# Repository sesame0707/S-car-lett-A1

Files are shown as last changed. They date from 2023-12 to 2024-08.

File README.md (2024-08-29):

# S(car)lett A1

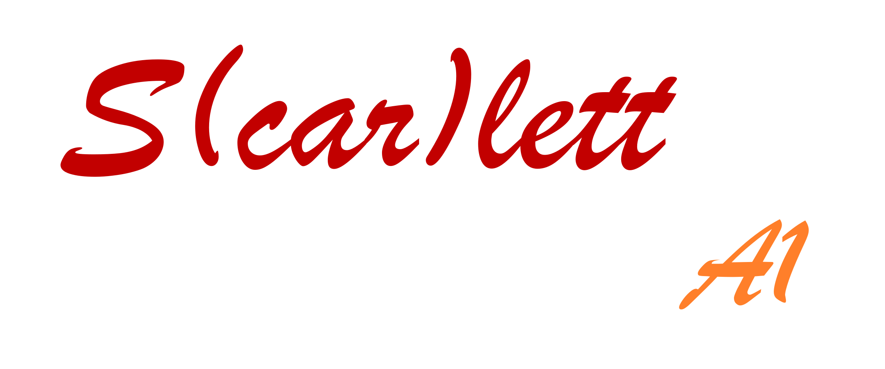
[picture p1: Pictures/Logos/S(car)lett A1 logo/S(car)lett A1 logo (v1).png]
S(car)lett A1 Logo


## The Repository
This is the repository of the first A-line car in the [`S(car)lett`](https://github.com/sesame0707/S-car-lett) project.

## High-Level Goals
Those are the initial goals of this module:
- The use of mechanical mechanisms implemented in the LEGO 8070 set
- Design focused on easy disassembly and assembly (reusable design)
- The use of more expensive, but desirable components instead of cheaper, but weaker ones

All of the above goals have been achieved throughout this module's implementation.

## Results
The car looks as follows:

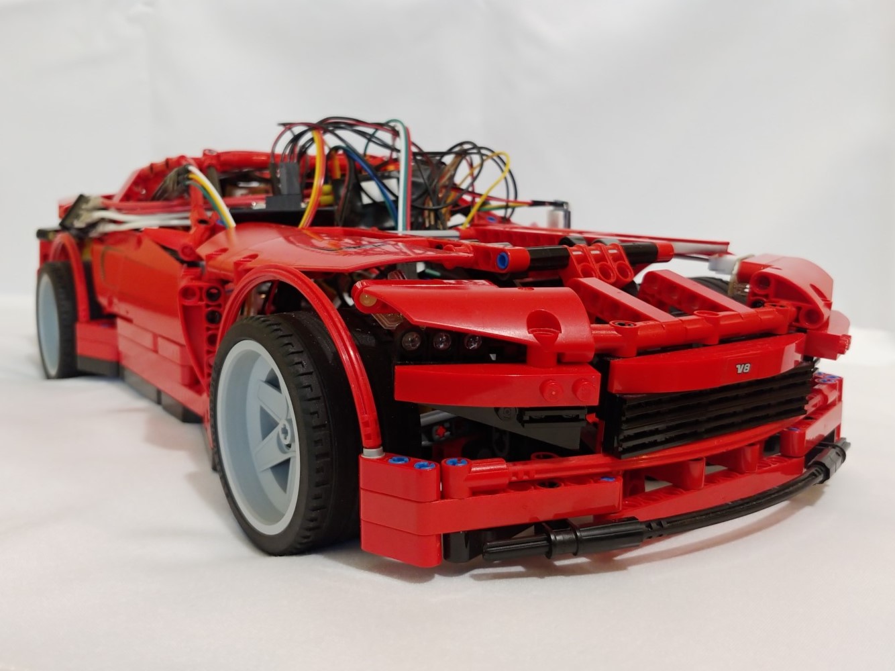
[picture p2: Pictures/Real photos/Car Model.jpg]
Car Model


It has some custom and standard electronic parts in it. The real photos of them can be accessed in the `Pictures/Real photos` folder. For the standard parts, refer to the table of parts that can be found in the `Documentation/General` folder. Moreover, this model also incorporates 3D-printed parts, which can be accessed in the `3D printed parts` folder.

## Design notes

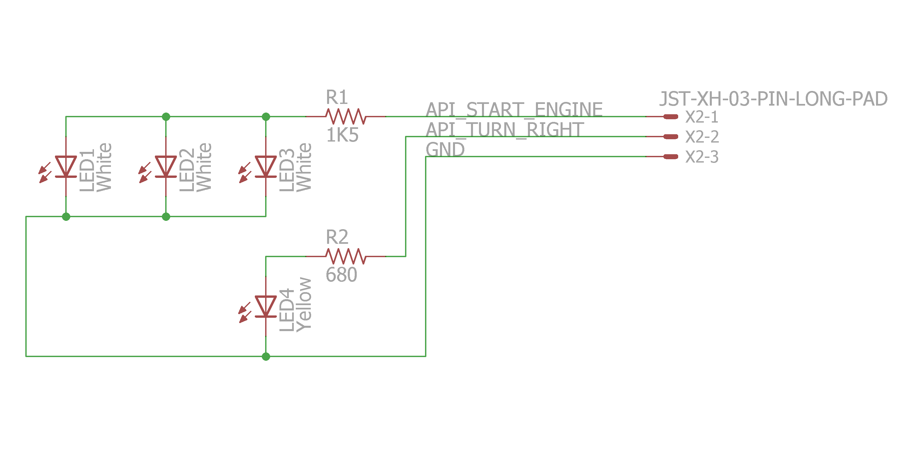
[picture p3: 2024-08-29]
Pictures/Electronic parts/Front Right Lamp (Schematic).png

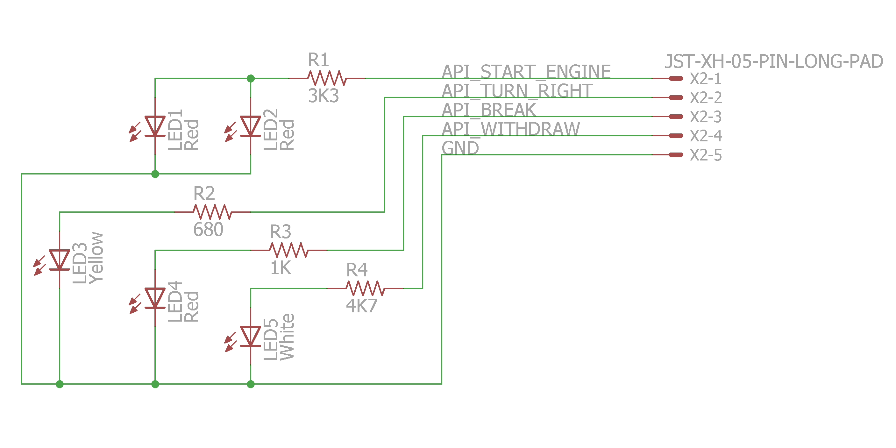
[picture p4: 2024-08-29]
Pictures/Electronic parts/Rear Right Lamp (Schematic).png

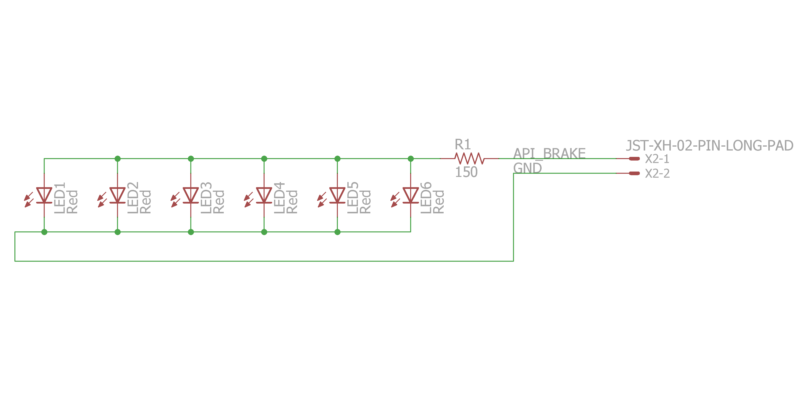
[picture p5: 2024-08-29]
Pictures/Electronic parts/Rear Brake Lamp (Schematic).png

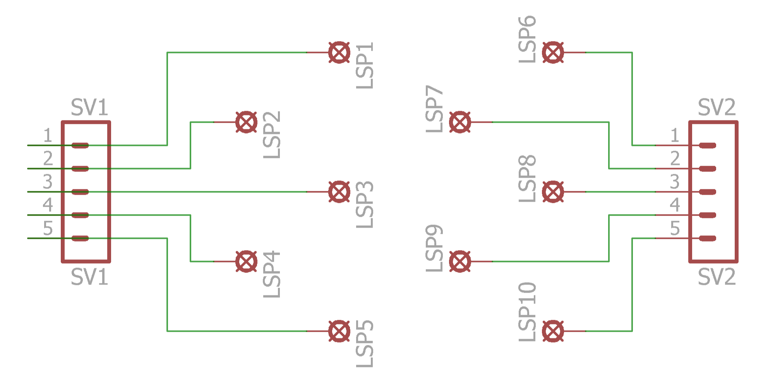
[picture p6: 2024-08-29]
Pictures/Electronic parts/Fuse Protector (Schematic).png

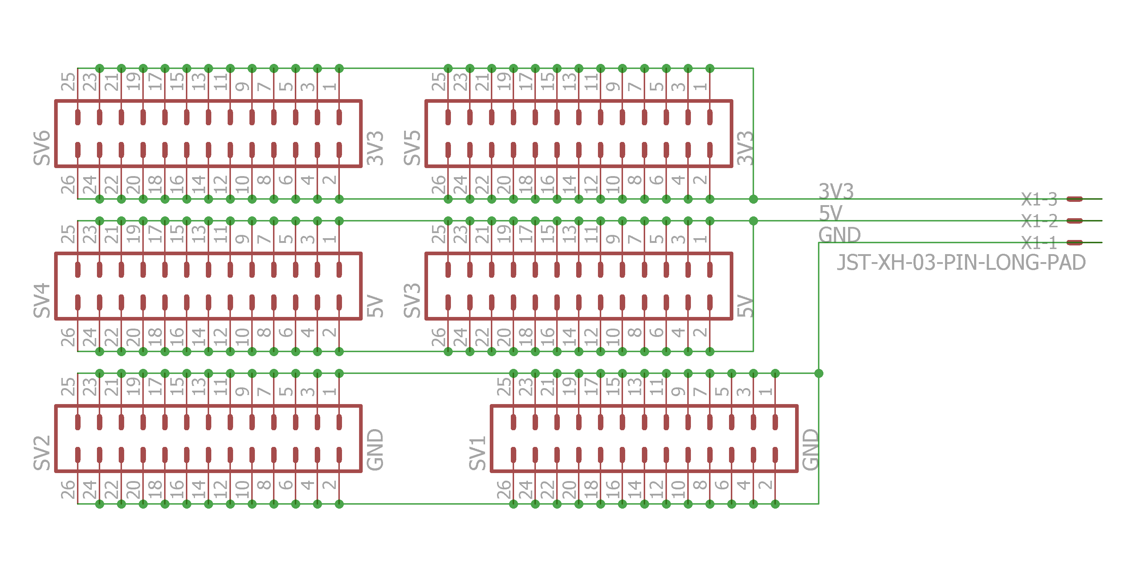
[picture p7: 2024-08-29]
Pictures/Electronic parts/STM32 Power Expander (Schematic).png

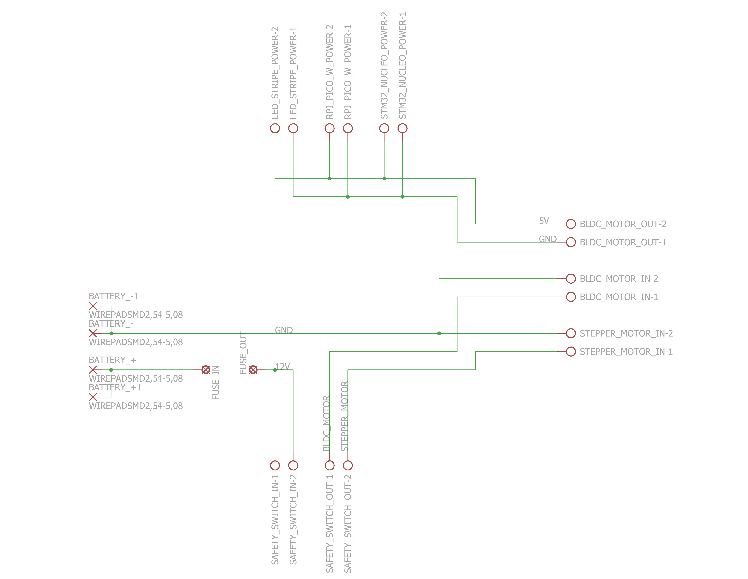
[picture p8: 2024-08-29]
Pictures/Electronic parts/Power Section (Schematic).png

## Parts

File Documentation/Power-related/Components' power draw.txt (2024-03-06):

Stepper motor
-------------
Inactive:		0.22 A @ 11 V = 2.42 W
Active:			0.72 A @ 11 V = 7.92 W

BLDC motor
----------
Without load:
-2 gear:		0.20 A @ 11 V = 2.20 W
-1 gear:		0.17 A @ 11 V = 1.87 W
0 gear:			0.01 A @ 11 V = 0.11 W
1 gear:			0.17 A @ 11 V = 1.87 W
2 gear:			0.20 A @ 11 V = 2.20 W
3 gear:			0.26 A @ 11 V = 2.86 W
4 gear:			0.27 A @ 11 V = 2.97 W

With load:		<= 0.50 A @ 11 V = 5.50 W

Voltmeter
---------
19.00 mA @ 12.60 V = 0.24 W
16.50 mA @ 11.00 V = 0.18 W
22.50 mA @ 9.00 V = 0.20 W

Battery level indicator
-----------------------
4.85 mA @ 12.60 V = 0.06 W
4.75 mA @ 11.00 V = 0.05 W
3.50 mA @ 9.00 V = 0.03 W

STM32 Nucleo
------------
Under load:		500 mA (?) @ 5 V = 2.50 W

	Lamps
	-----
	Start engine: 		1.6 mA
	Turn left: 		4.0 mA
	Turn right: 		4.0 mA
	Brake: 			12.0 mA
	Withdraw: 		0.3 mA
	
	All lamps:		21.9 mA @ 3.3 V = 0.07 W

RPi Pico W
----------
Under load:		100 mA @ 5 V = 0.50 W

LED stripes
-----------
All 14x sub-LEDs:	0.43 A @ 5 V = 2.15 W

Rechargeable battery
--------------------
Brand:			Sunpadow
Type:			Li-Po
Energy capacity:	24.98 Wh
Charge capacity:	2250 mAh
Cells:			3S-ERC
Maximum power output:	60C
Charge power input:	1C
Nominal total voltage:	11.1 V
Allowed total voltage:	9.0 V - 12.6 V

Current x charge level
----------------------
0 % (9.0 V):		1.52 A + 0.60 A = 2.12 A
25 % (10.2 V):		1.35 A + 0.53 A = 1.88 A
50 % (10.8 V):		1.27 A + 0.50 A = 1.77 A
75 % (11.4 V):		1.21 A + 0.47 A = 1.68 A
100 % (12.6 V):		1.10 A + 0.43 A = 1.53 A

Recommended fuses
-----------------
11 V main line:		2.50 A
5 V main line:		1.25 A
5 V STM32 line:		0.25 A
3.3 V STM32 line:	0.25 A

Summary
-------
Maximum total power draw:		13.72 W (11 V main line) + 5.40 W (?) (5 V main line) = 18.82 W
Theoretical minimum working time:	1.33 h (1 h 20 min) (?)
Theoretical average working time:	2.66 h (2 h 40 min) (?)

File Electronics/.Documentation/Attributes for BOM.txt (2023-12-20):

Attributes for BOM
Common:-----------------
MANUFACTURER
	LUCKYLIGHT
	ROYAL OHM
MANUFACTURER_PART_NUMBER
SUPPLIER
	TME
SUPPLIER_PART_NUMBER
SUPPLIER_URL

LED-specific:-----------
COLOR
CURRENT_EMPIRICAL
VOLTAGE_EMPIRICAL

Resistor-specific:------
RESISTANCE

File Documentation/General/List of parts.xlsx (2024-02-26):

PART NAME | QTY. | STATUS | PRICE (1 PCS.) | PRICE (ALL PCS.) | PRICE DATE | LINK | SELLER | PROJECT PRICE
LEGO 8070 "Supercar" set | 1 | Ready | 400.00 zł | 400.00 zł | 2011-07-07 | https://www.ceneo.pl/9803476 | Authorized LEGO reseller | 1849.65 zł
Nema 17 (23,5 mm) stepper motor | 1 | Ready | 35.00 zł | 35.00 zł | 2023-05-06 | https://allegro.pl/oferta/silnik-krokowy-nema17-17hs4023-z-kablem-1m-prusa-13093450848 | Allegro (sklep_X3D)
TMC2209 stepper motor driver | 1 | Ready | 28.50 zł | 28.50 zł | 2023-05-06 | https://allegro.pl/oferta/sterownik-silnika-krokowego-tmc2209-v1-3-stepstick-13629864488 | Allegro (sklep_X3D)
GT2 belt (6 mm, 1 m) | 1 | Ready | 6.99 zł | 6.99 zł | 2023-05-06 | https://allegro.pl/oferta/pasek-zebaty-gumowy-gt2-6mm-napedowy-cnc-100cm-12872474627 | Allegro (sklep_X3D)
GT2 overlay for stepper motor (20 T, 10 mm) | 1 | Ready | 9.90 zł | 9.90 zł | 2023-05-06 | https://allegro.pl/oferta/kolo-pasowe-zebate-20-zebow-otwor-6mm-gt2-10mm-12588977251 | Allegro (sklep_X3D)
Zip ties (2,5 mm x 100 mm ⌀ 3 mm 100 pcs.) | 1 | Ready | 2.69 zł | 2.69 zł | 2023-07-17 | https://allegro.pl/oferta/opaski-zaciskowe-kablowe-trytytki-100x2-5mm-100szt-13133446154 | Allegro (sklep_X3D)
Nema 17 radiator | 1 | Ready | 6.99 zł | 6.99 zł | 2023-07-17 | https://allegro.pl/oferta/radiator-silnika-krokowego-40x40x11-czarny-nema17-12867637945 | Allegro (sklep_X3D)
Coupler (5 mm, 8 mm) | 1 | Ready | 5.99 zł | 5.99 zł | 2023-07-17 | https://allegro.pl/oferta/sprzeglo-elastyczne-5x8-aluminiowe-cnc-13094635538 | Allegro (sklep_X3D)
STM32 NUCLEO-F767ZI developer board | 1 | Ready | 145.00 zł | 145.00 zł | 2023-08-10 | https://allegro.pl/oferta/stm32-nucleo-f767zi-stm32f767zit6-arm-cortex-m7-14034014339 | Allegro (botland_pl)
JST-SM 2/3/4/5 pin header set | 1 | Ready | 31.00 zł | 31.00 zł | 2023-08-17 | https://allegro.pl/oferta/zestaw-zlacz-justpi-jst-sm-2-3-4-5pin-11787730550 | Allegro (botland_pl)
USB A male connector (5 pcs.) | 1 | Ready | 3.00 zł | 3.00 zł | 2023-08-17 | https://allegro.pl/oferta/gniazdo-usb-typu-a-zenskie-tht-5szt-12551145487 | Allegro (botland_pl)
USB micro B - USB A 2.0 (0,15 m) cable | 1 | Ready | 4.00 zł | 4.00 zł | 2023-08-17 | https://allegro.pl/oferta/przewod-microusb-b-usb-a-2-0-hi-speed-0-15-m-14012907744 | Allegro (botland_pl)
WS2812B LED stripe (60 LED/m, IP65, 1 m) | 1 | Ready | 32.90 zł | 32.90 zł | 2023-08-17 | https://allegro.pl/oferta/tasma-led-adresowalna-ws2812b-argb-60led-m-ip65-13796044103 | Allegro (Minosalis)
JST-SM 3 pin LED male and female cable set (15 cm) | 4 | Ready | 3.50 zł | 14.00 zł | 2023-08-17 | https://allegro.pl/oferta/wtyczka-jst-sm-3-pin-led-argb-meska-i-zenska-15-cm-13821206609 | Allegro (Minosalis)
JST-SM 3 pin LED splitter (15 cm) | 1 | Ready | 10.90 zł | 10.90 zł | 2023-08-17 | https://allegro.pl/oferta/rozdzielacz-jst-sm-3-pin-do-led-argb-13821309653 | Allegro (Minosalis)
Imax B6AC 80W charger | 1 | Ready | 134.78 zł | 134.78 zł | 2023-08-17 | https://allegro.pl/oferta/ladowarka-b6ac-z-balanserem-do-pakietow-13584815585 | Allegro (kamami_pl)
Sunpadow Li-Po battery (3S, 11,1 V, 60 C, 2250 mAh, XT60) | 1 | Ready | 104.57 zł | 104.57 zł | 2023-08-17 | https://www.amazon.pl/dp/B08S3C9C5M?psc=1&ref=ppx_yo2ov_dt_b_product_details | Amazon (Xiamen 3-circles Battery Co., Ltd.)
40A ESC and 1000KV BLDC motor set | 1 | Ready | 73.55 zł | 73.55 zł | 2023-08-17 | https://www.amazon.pl/gp/product/B08T6CNVQT/ref=ppx_od_dt_b_asin_title_s00?ie=UTF8&psc=1 | Amazon (Yisteel-EU)
VL53L1X ToF module | 4 | Ready | 19.39 zł | 77.56 zł | 2023-09-04 | https://pl.aliexpress.com/item/4000074204979.html | AliExpress (SAMIORE Store)
Electric cubes (12 x 2,5 mm2) | 3 | Ready | 1.57 zł | 4.71 zł | 2023-09-04 | https://allegro.pl/oferta/listwa-zaciskowa-zlaczka-kostka-12-torowa-2-5mm2-8501387810 | Allegro (electro_24)
Electric cubes (12 x 4 mm2) | 1 | Ready | 1.89 zł | 1.89 zł | 2023-09-04 | https://allegro.pl/oferta/zlaczka-listwa-instalacyjna-kablowa-12-torowa-4mm-7270241593 | Allegro (electro_24)
Tubular terminals set | 1 | Ready | 54.90 zł | 54.90 zł | 2023-09-04 | https://allegro.pl/oferta/zaciskarka-do-konektorow-koncowek-500-tulejek-13993749597 | Allegro (electro_24)
Universal PCB set | 1 | Ready | 33.99 zł | 33.99 zł | 2023-09-04 | https://www.amazon.pl/gp/product/B07V25W5RT | Amazon (AZDelivery)
IR module set | 1 | Ready | 20.49 zł | 20.49 zł | 2023-09-04 | https://www.amazon.pl/gp/product/B07V9XD2R6 | Amazon (AZDelivery)
Raspberry Pi Pico W enclosure (transparent) | 1 | Ready | 6.90 zł | 6.90 zł | 2023-09-12 | https://allegro.pl/oferta/obudowa-raspberry-pi-pico-transparentna-13052332067 | Allegro (Platet-A)
Security ON/OFF switch | 1 | Ready | 4.00 zł | 4.00 zł | 2023-09-12 | https://allegro.pl/oferta/przelacznik-klawiszowy-on-off-250v-kcd1-104-6a-12386835341 | Allegro (Platet-A)
OLED display (I2C, 0.96 in) | 1 | Ready | 20.00 zł | 20.00 zł | 2023-09-12 | https://allegro.pl/oferta/wyswietlacz-oled-0-96-cala-i2c-iic-4-pin-bialy-13396251090 | Allegro (Platet-A)
XT60 male connector with AWG12 wires | 1 | Ready | 15.50 zł | 15.50 zł | 2023-09-12 | https://allegro.pl/oferta/wtyk-xt60-meski-z-przewodem-10cm-awg12-14093751536 | Allegro (Platet-A)
XT60 female connector with AWG12 wires | 1 | Ready | 15.50 zł | 15.50 zł | 2023-09-12 | https://allegro.pl/oferta/gniazdo-xt60-z-przewodem-10cm-awg12-zenskie-14091453758 | Allegro (Platet-A)
LED diodes set (100 pcs.) | 1 | Ready | 12.00 zł | 12.00 zł | 2023-09-12 | https://allegro.pl/oferta/zestaw-diod-led-5mm-rgb-biale-100szt-mix-13396031473 | Allegro (Platet-A)
ARK 3 pin connector | 10 | Ready | 1.50 zł | 15.00 zł | 2023-09-12 | https://allegro.pl/oferta/konektor-listwa-ak-ark-5-0mm-h-10mm-3-pin-x-2szt-10420014477 | Allegro (Platet-A)
Male goldpin (2,54mm, 2x40) | 2 | Ready | 3.00 zł | 6.00 zł | 2023-09-12 | https://allegro.pl/oferta/listwa-gold-pin-2x40-meska-tht-2-54mm-prosta-10248104944 | Allegro (Platet-A)
Female goldpin (2,54mm, 1x40) | 4 | Ready | 3.00 zł | 12.00 zł | 2023-09-12 | https://allegro.pl/oferta/gniazdo-szplikowe-goldpin-raster-2-54mm-1x40-10248060552 | Allegro (Platet-A)
Resistors set (700 pcs.) | 1 | Ready | 22.90 zł | 22.90 zł | 2023-09-12 | https://allegro.pl/oferta/zestaw-rezystorow-przewlekanych-0-25w-1-700-sztuk-13498410400 | Allegro (Platet-A)
Female goldpin (2,54mm, 2x40) | 2 | Ready | 1.30 zł | 2.60 zł | 2023-10-19 | https://allegro.pl/oferta/listwa-goldpin-2x40-zenska-raster-2-54mm-10szt-12327613595 | Allegro (botland_pl)
Male goldpin (2,54mm, 2x40, curved) | 2 | Ready | 2.00 zł | 4.00 zł | 2023-10-19 | https://allegro.pl/oferta/wtyk-goldpin-2x40-katowy-raster-2-54mm-14376476217 | Allegro (botland_pl)
JST-XH 2-5 pin connector set (230 pcs.) | 1 | Ready | 25.00 zł | 25.00 zł | 2023-10-19 | https://allegro.pl/oferta/zestaw-zlacz-jst-xh2-54-meskie-zenskie-i-pinow-11032577415 | Allegro (botland_pl)
JST-XH 6-10 pin connector set (260 pcs.) | 1 | Ready | 31.00 zł | 31.00 zł | 2023-10-19 | https://allegro.pl/oferta/zestaw-zlacz-jst-xh2-54-6-7-8-9-10-pin-2-54mm-12635826639 | Allegro (botland_pl)
Male goldpin (2,54mm, 1x40, curved) | 4 | Ready | 2.00 zł | 8.00 zł | 2023-10-19 | https://allegro.pl/oferta/goldpin-czarny-1x40-szpil-katowy-raster-2-54mm-13410442465 | Allegro (kamami_pl)
Male goldpin (2,54mm, 1x40) | 4 | Ready | 1.70 zł | 6.80 zł | 2023-10-19 | https://allegro.pl/oferta/goldpin-czarny-1x40-szpil-prosty-raster-2-54mm-13717595094 | Allegro (kamami_pl)
VL53L1X ToF module | 4 | Ready | 17.57 zł | 70.28 zł | 2023-11-27 | https://pl.aliexpress.com/item/4000074204979.html | AliExpress (SAMIORE Store)
ZS-X10 V3 BLDC motor driver | 1 | Ready | 44.75 zł | 44.75 zł | 2023-12-01 | https://allegro.pl/oferta/sterownik-silnikow-bldc-6-20v-3a-13359462424 | Allegro (kamami_pl)
PTF-76 fuse holder | 1 | Ready | 1.85 zł | 1.85 zł | 2023-12-07 | https://allegro.pl/oferta/oprawa-bezpiecznika-5x20mm-ptf-76-z-uchwytem-1727-10001770448 | Allegro (tomsyty)
ARK 2 pin connector | 30 | Ready | 0.60 zł | 18.00 zł | 2023-12-08 | https://allegro.pl/oferta/zlacze-ark-2-pin-5-08mm-5-szt-0693-5-10912515733 | Allegro (tomsyty)
3A fuse (5 x 20mm, fast, 10 pcs.) | 1 | Ready | 1.85 zł | 1.85 zł | 2023-12-08 | https://allegro.pl/oferta/bezpiecznik-5x20mm-szybki-3a-10-szt-0602-10-9510464377 | Allegro (tomsyty)
SMD resistor (1206, 100 Ohm, 50 pcs.) | 1 | Ready | 2.00 zł | 2.00 zł | 2023-12-08 | https://allegro.pl/oferta/rezystory-smd-1206-100r-101-50-szt-4425-50-12684715501 | Allegro (tomsyty)
SMD resistor (1206, 680 Ohm, 50 pcs.) | 1 | Ready | 2.00 zł | 2.00 zł | 2023-12-08 | https://allegro.pl/oferta/rezystory-smd-1206-680r-681-50-szt-4439-50-12684756050 | Allegro (tomsyty)
SMD resistor (1206, 1000 Ohm, 50 pcs.) | 1 | Ready | 2.00 zł | 2.00 zł | 2023-12-08 | https://allegro.pl/oferta/rezystory-smd-1206-1k-102-50-szt-4441-50-12684760810 | Allegro (tomsyty)
SMD resistor (1206, 1500 Ohm, 50 pcs.) | 1 | Ready | 2.00 zł | 2.00 zł | 2023-12-08 | https://allegro.pl/oferta/rezystory-smd-1206-1-5k-152-50-szt-4443-50-12684768996 | Allegro (tomsyty)
SMD resistor (1206, 3300 Ohm, 50 pcs.) | 1 | Ready | 2.00 zł | 2.00 zł | 2023-12-08 | https://allegro.pl/oferta/rezystory-smd-1206-3-3k-332-50-szt-4449-50-12684791144 | Allegro (tomsyty)
SMD resistor (1206, 4700 Ohm, 50 pcs.) | 1 | Ready | 2.05 zł | 2.05 zł | 2023-12-08 | https://allegro.pl/oferta/rezystory-smd-1206-4-7k-472-50-szt-4452-50-12684801225 | Allegro (tomsyty)
Goldpin 1 pin socket (10 pcs.) | 2 | Ready | 1.55 zł | 3.10 zł | 2023-12-08 | https://allegro.pl/oferta/gniazdo-na-goldpin-styki-bls-01-10-szt-0092-10-11597011191 | Allegro (tomsyty)
Goldpin 2 pin socket (10 pcs.) | 1 | Ready | 2.00 zł | 2.00 zł | 2023-12-08 | https://allegro.pl/oferta/gniazdo-na-goldpin-styki-bls-02-10-szt-0094-10-11571011242 | Allegro (tomsyty)
Goldpin 4 pin socket (10 pcs.) | 1 | Ready | 1.95 zł | 1.95 zł | 2023-12-08 | https://allegro.pl/oferta/gniazdo-na-goldpin-styki-bls-04-5-szt-0096-5-10411158259 | Allegro (tomsyty)
Goldpin male pins (25 pcs.) | 2 | Ready | 2.00 zł | 4.00 zł | 2023-12-08 | https://allegro.pl/oferta/piny-meskie-do-gniazd-bls-bld-25-szt-2076-25-13810658015 | Allegro (tomsyty)
Car connector (6,3mm, 10 pcs.) | 1 | Ready | 2.65 zł | 2.65 zł | 2023-12-08 | https://allegro.pl/oferta/konektor-samochodowy-meski-6-3mm-10szt-0776-10-12650703236 | Allegro (tomsyty)
Car connector cover (6,3mm, 10 pcs.) | 1 | Ready | 1.40 zł | 1.40 zł | 2023-12-08 | https://allegro.pl/oferta/oslona-konektora-6-3mm-elast-10-szt-0108-10-11976191253 | Allegro (tomsyty)
Color IDC tape (AWG28, 14 wires, 1m) | 2 | Ready | 6.00 zł | 12.00 zł | 2023-12-10 | https://allegro.pl/oferta/tasma-idc-kolor-14-zyl-awg28-do-zlacz-idc-1mb-14376104118 | Allegro (ABC-RC_pl)
M2 screw, nut, pad set (420 pcs., black, metal) | 1 | Ready | 34.90 zł | 34.90 zł | 2023-12-10 | https://allegro.pl/oferta/zestaw-420szt-metalowych-srub-nakretek-m2-czarny-14336632344 | Allegro (ABC-RC_pl)
Heat shrink tubing set (1-14mm, 164 pcs.) | 1 | Ready | 7.40 zł | 7.40 zł | 2023-12-10 | https://allegro.pl/oferta/zestaw-164-szt-rurek-termokurczliwych-kolor-1-do-14-mm-rurka-termokur-14506103695 | Allegro (ABC-RC_pl)
Cable braid (2mm/4mm, 1m, black) | 1 | Ready | 1.90 zł | 1.90 zł | 2023-12-10 | https://allegro.pl/oferta/oplot-na-przewody-2mm-4mm-poliestrowy-black-1mb-14328317633 | Allegro (ABC-RC_pl)
Cable braid (3mm/6mm, 1m, black) | 1 | Ready | 1.80 zł | 1.80 zł | 2023-12-10 | https://allegro.pl/oferta/oplot-na-przewody-3mm-6mm-poliestrowy-black-1mb-14328317448 | Allegro (ABC-RC_pl)
Cable braid (4mm/8mm, 1m, black) | 1 | Ready | 2.00 zł | 2.00 zł | 2023-12-10 | https://allegro.pl/oferta/oplot-na-przewody-4mm-8mm-poliestrowy-black-1mb-14328193326 | Allegro (ABC-RC_pl)
Cable braid (5mm/10mm, 1m, black) | 1 | Ready | 2.00 zł | 2.00 zł | 2023-12-10 | https://allegro.pl/oferta/oplot-na-przewody-5mm-10mm-poliestrowy-black-1mb-14328186594 | Allegro (ABC-RC_pl)
Mounting tape (16mm, 2m, 2mm, white) | 1 | Ready | 6.80 zł | 6.80 zł | 2023-12-10 | https://allegro.pl/oferta/tasma-piankowa-dwustronna-16mm-x-2m-montazowa-11886077539 | Allegro (handlo_net)
Banan 3.5mm connector with wire set (female+male) | 4 | Ready | 6.14 zł | 24.56 zł | 2023-12-10 | https://allegro.pl/oferta/wtyczka-gniazdo-banan-3-5mm-syma-x8-walkera-6785678261 | Allegro (handlo_net)
Lithium battery charge indicator (1S-8S, 5 mA, green) | 1 | Ready | 9.60 zł | 9.60 zł | 2024-02-01 | https://allegro.pl/oferta/wskaznik-naladowania-akumulatora-li-ion-uniwersalny-zielony-32-x-20-mm-13040945266 | Allegro (msalamon_pl)
JST 2 pin male connector with wires | 5 | Ready | 1.50 zł | 7.50 zł | 2024-02-14 | https://allegro.pl/oferta/zlacze-jst-meskie-2pin-z-przewodem-10cm-12315481475 | Allegro (ZBYROMEX)
JST 2 pin female connector with wires | 5 | Ready | 1.50 zł | 7.50 zł | 2024-02-14 | https://allegro.pl/oferta/zlacze-jst-zenskie-2pin-z-przewodem-10cm-13941127737 | Allegro (ZBYROMEX)
Male XT60 -> female DEAN-T adapter | 1 | Ready | 11.00 zł | 11.00 zł | 2024-02-14 | https://allegro.pl/oferta/adapter-zlacze-xt60-meskie-zlacze-dean-t-zen-12815880539 | Allegro (ZBYROMEX)
Female XT60 -> male DEAN-T adapter | 1 | Ready | 13.00 zł | 13.00 zł | 2024-02-14 | https://allegro.pl/oferta/adapter-zlacze-xt60-zenskie-zlacze-dean-t-me-12815894905 | Allegro (ZBYROMEX)
YX-X801 battery deep discharge protector (12 V DC, 10 A) | 1 | Ready | 22.60 zł | 22.60 zł | 2024-02-14 | https://allegro.pl/oferta/zabezpieczenie-przed-rozladowaniem-akumulatora-12v-11446448483 | Allegro (OMEGA_ZONE)
Bi-directional logic level converter (4 CH) | 4 | Ready | 4.27 zł | 17.08 zł | 2024-02-14 | https://allegro.pl/oferta/konwerter-poziomow-logicznych-3-3-5v-dwustronny-11825109052 | Allegro (msalamon_pl)
LED DC voltmeter (4-15 V DC, 30 mA, 100 kOhm, red) | 1 | Ready | 11.03 zł | 11.03 zł | 2024-02-14 | https://allegro.pl/oferta/woltomierz-dc-led-miernik-0-28-czerwony-13614436672 | Allegro (msalamon_pl)
Raspberry Pi Pico W | 1 | Ready | 34.61 zł | 34.61 zł | 2024-02-22 | https://allegro.pl/oferta/raspberry-pi-pico-w-12351876204 | Allegro (kamami_pl)
DC-DC step-down converter (7-26 Vin, 5 Vout, max 3 A) | 1 | Ready | 7.99 zł | 7.99 zł | 2024-02-26 | https://allegro.pl/oferta/modul-przetwornicy-dc-dc-step-down-5v-3a-13098360936 | Allegro (kamami_pl)

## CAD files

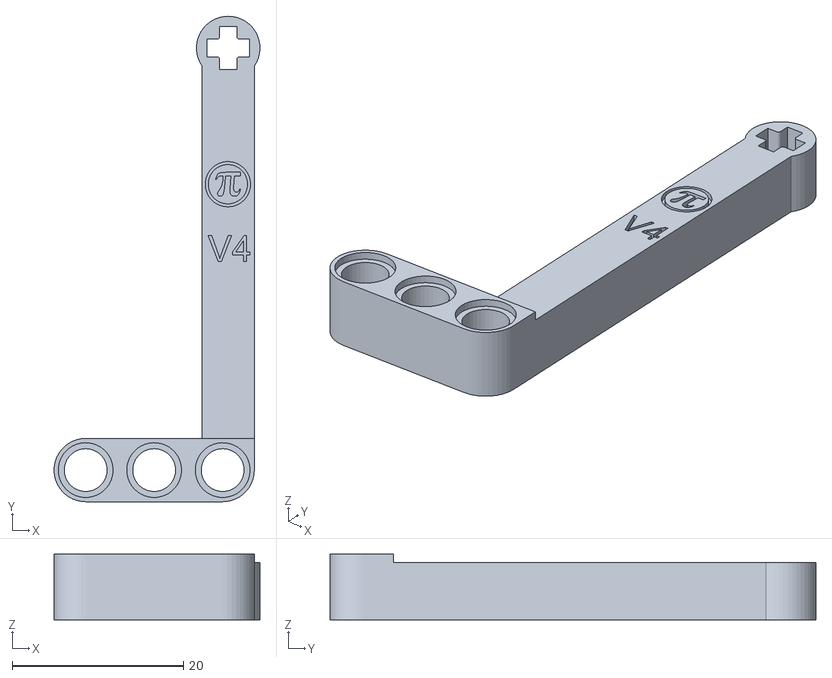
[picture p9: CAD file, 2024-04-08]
3D printed parts/1. Stepper motor holder (L)/1. Stepper motor holder (L) [V4].stl
24.1 x 56.7 x 7.70

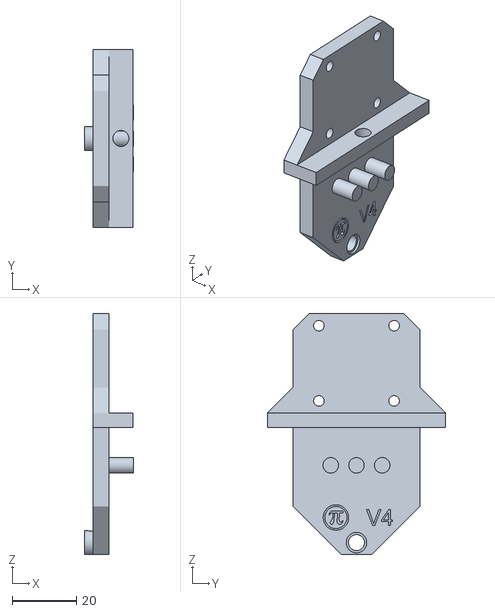
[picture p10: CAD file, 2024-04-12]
3D printed parts/3. BLDC motor holder/3. BLDC motor holder [V4].stl
15.4 x 55.5 x 75.0

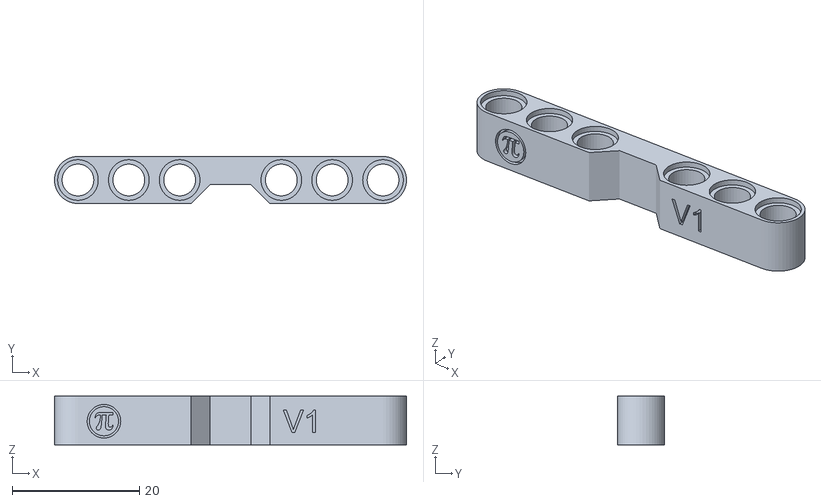
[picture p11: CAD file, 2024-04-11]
3D printed parts/4. BLDC motor transmission 7x bar/4. BLDC motor transmission 7x bar [V1].stl
55.4 x 7.40 x 7.70

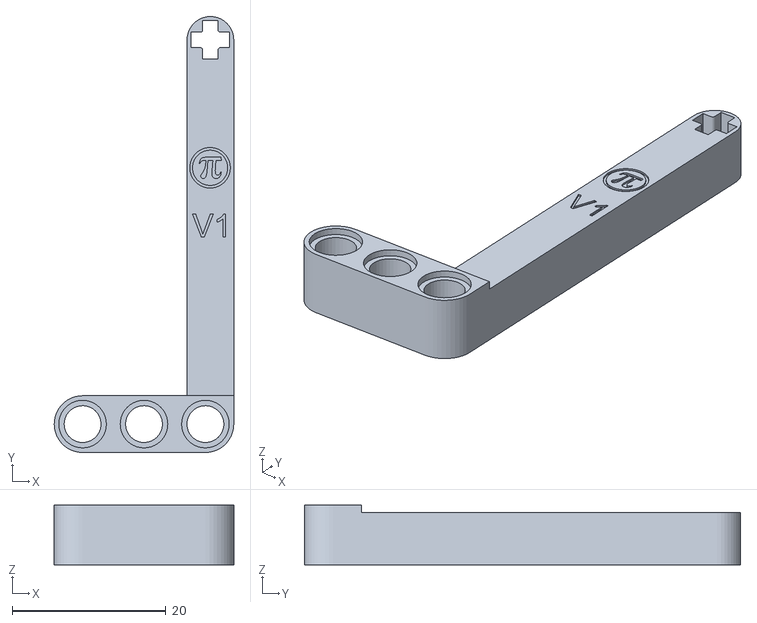
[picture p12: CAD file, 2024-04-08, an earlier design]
3D printed parts/1. Stepper motor holder (L)/1. Stepper motor holder (L) [V1].stl
23.4 x 56.8 x 7.80

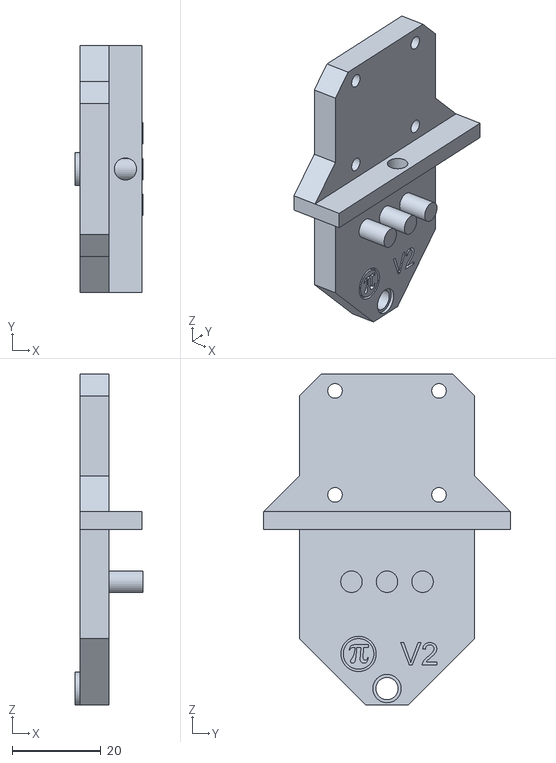
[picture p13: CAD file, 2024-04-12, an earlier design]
3D printed parts/3. BLDC motor holder/3. BLDC motor holder [V2].stl
15.4 x 55.5 x 74.5

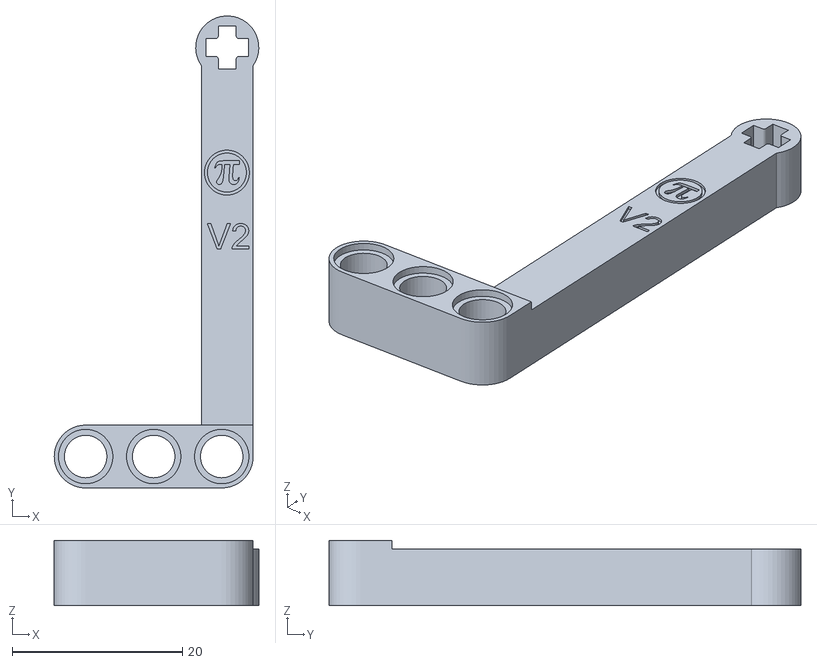
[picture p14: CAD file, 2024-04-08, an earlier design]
3D printed parts/1. Stepper motor holder (L)/1. Stepper motor holder (L) [V2].stl
24.1 x 55.5 x 7.70

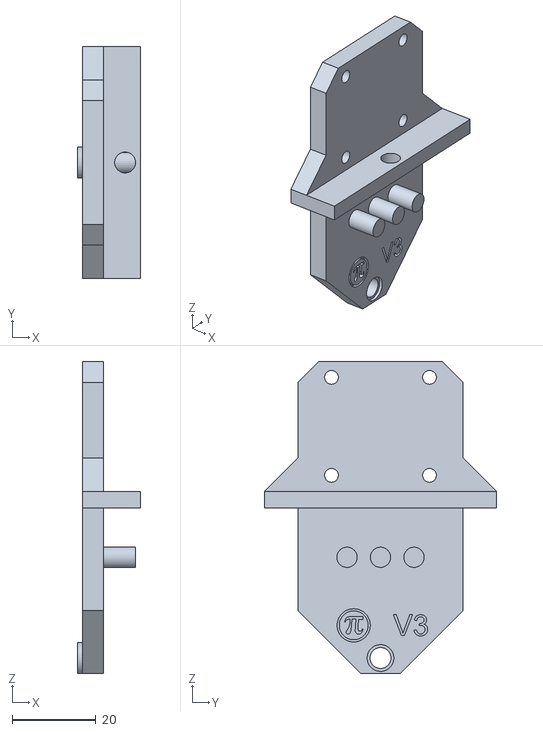
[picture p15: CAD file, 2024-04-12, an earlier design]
3D printed parts/3. BLDC motor holder/3. BLDC motor holder [V3].stl
15.1 x 55.5 x 74.5

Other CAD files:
3D printed parts/2. Stepper motor holder (R)/2. Stepper motor holder (R) [V4].stl
3D printed parts/1. Stepper motor holder (L)/1. Stepper motor holder (L) [V3].stl
3D printed parts/3. BLDC motor holder/3. BLDC motor holder [V1].stl
3D printed parts/1. Stepper motor holder (L)/1. Stepper motor holder (L) [V1].f3d
3D printed parts/1. Stepper motor holder (L)/1. Stepper motor holder (L) [V2].f3d
3D printed parts/1. Stepper motor holder (L)/1. Stepper motor holder (L) [V3].f3d
3D printed parts/1. Stepper motor holder (L)/1. Stepper motor holder (L) [V4].f3d
3D printed parts/2. Stepper motor holder (R)/2. Stepper motor holder (R) [V4].f3d
3D printed parts/3. BLDC motor holder/3. BLDC motor holder [V1].f3d
3D printed parts/3. BLDC motor holder/3. BLDC motor holder [V2].f3d
3D printed parts/3. BLDC motor holder/3. BLDC motor holder [V3].f3d
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

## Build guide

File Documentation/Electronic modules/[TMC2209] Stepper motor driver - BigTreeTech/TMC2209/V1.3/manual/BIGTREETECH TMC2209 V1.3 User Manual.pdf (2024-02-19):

# TMC2209 V1.3

# User Manual

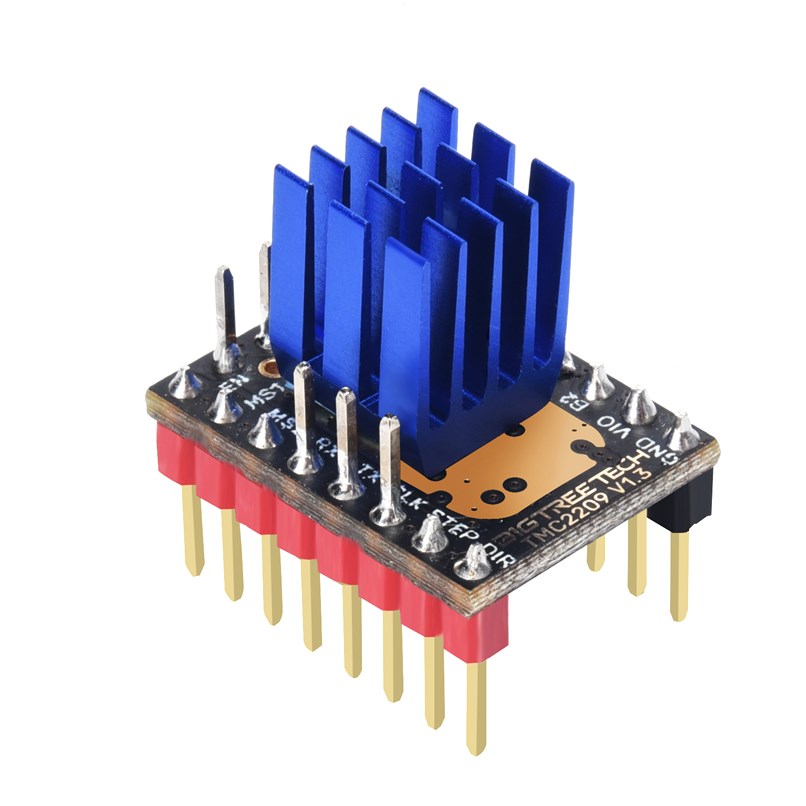
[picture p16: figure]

BIGTREETECH TMC2209 V1.3 User Manual

2

## Revision Log

Version | Date | Revisions
v1.00 | January 26th, 2024 | Initial Version

3

## CONTENTS

4

## Product Profile

The BIGTREETECH TMC2209 is a highly efficient stepper motor driver known for its silent operation. It's designed to handle a broad range of voltages and can support significant current output.

Specifications

- Microstepping Capability: 256 microsteps
- Voltage Range: DC 12V – DC 28V
- Peak Current Support: 2A
- Sensorless Homing: Supported
- Low on-resistance: Rdson(H+L)=340mΩ
- Communication: UART (default)
- Multiprotection: Overheat, overvoltage and stall protection.

Dimension

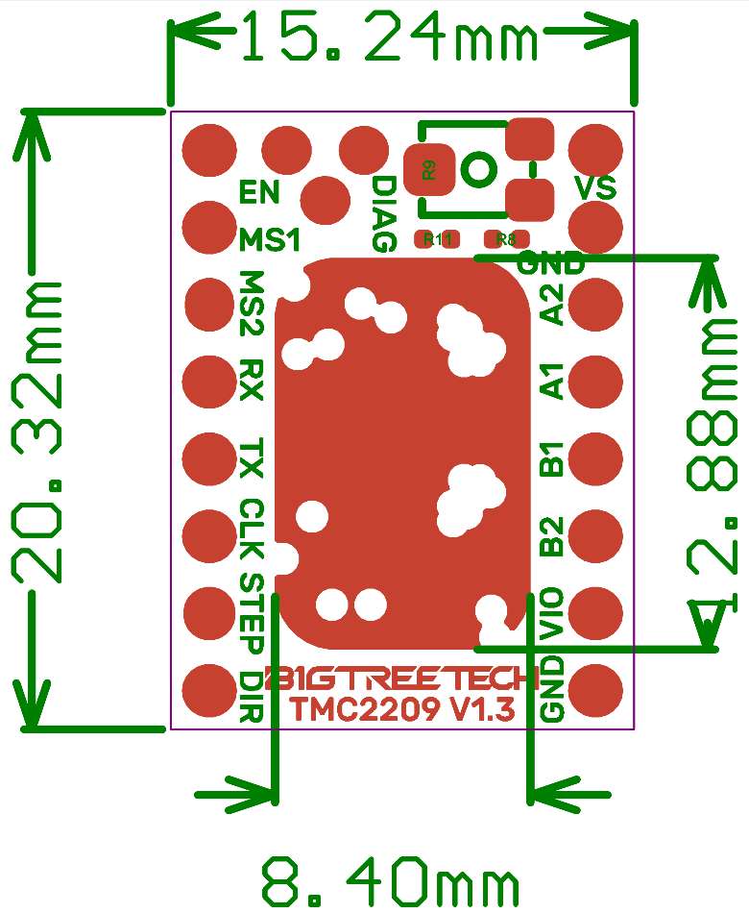
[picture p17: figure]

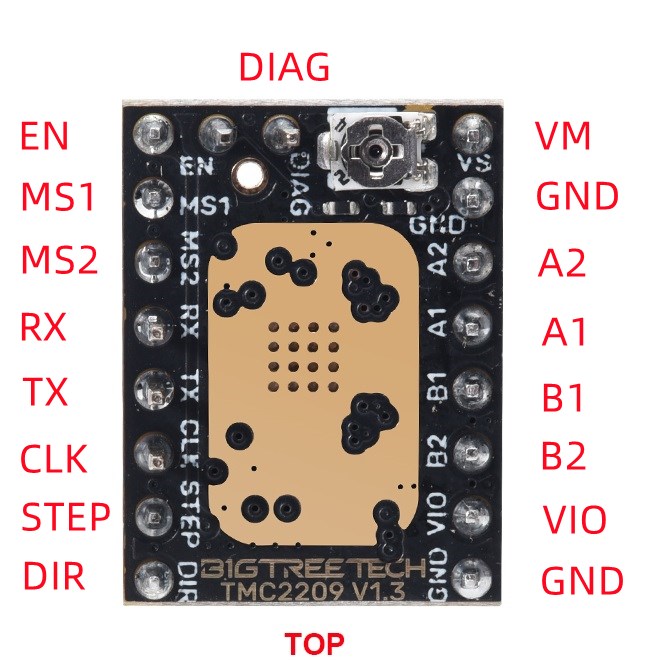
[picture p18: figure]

5

## Peripheral Interface

Pin Description

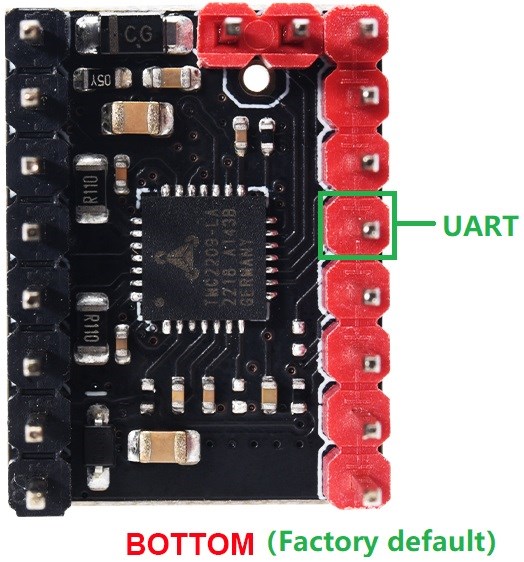
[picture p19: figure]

6

## Example of Use

Mode Selection

The default mode is UART as shown below:

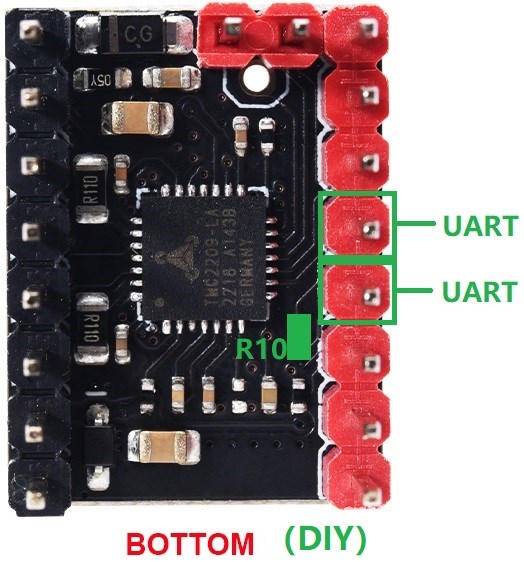
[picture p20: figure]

7

To alter UART pin assignments for compatibility with different boards, solder the two pads at R10 together as shown:

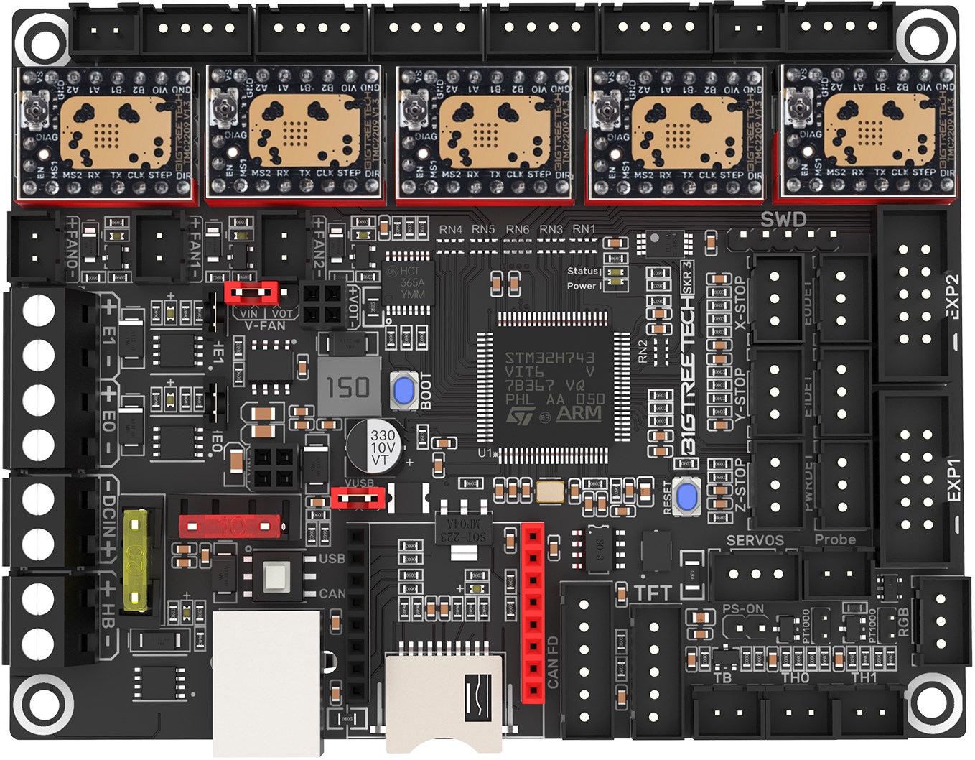
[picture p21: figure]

8

Using with SKR 3

## Safety Precautions

1. Ensure the driver is inserted in the correct direction to prevent damage.
2. Use active cooling when operating at high currents (above 1.2A) to prevent overheating.
3. If you're inexperienced with soldering, it's advised not to attempt it to avoid potential injuries.

If you need further resources for this product, you can find them at [GitHub](https://github.com/bigtreetech/). If you cannot find what you need, you may contact our after-sales support(service005@biqu3d.com).

If you encounter any other problems during use or have suggestions or feedback, please contact us. Thank you for choosing BIGTREETECH products.

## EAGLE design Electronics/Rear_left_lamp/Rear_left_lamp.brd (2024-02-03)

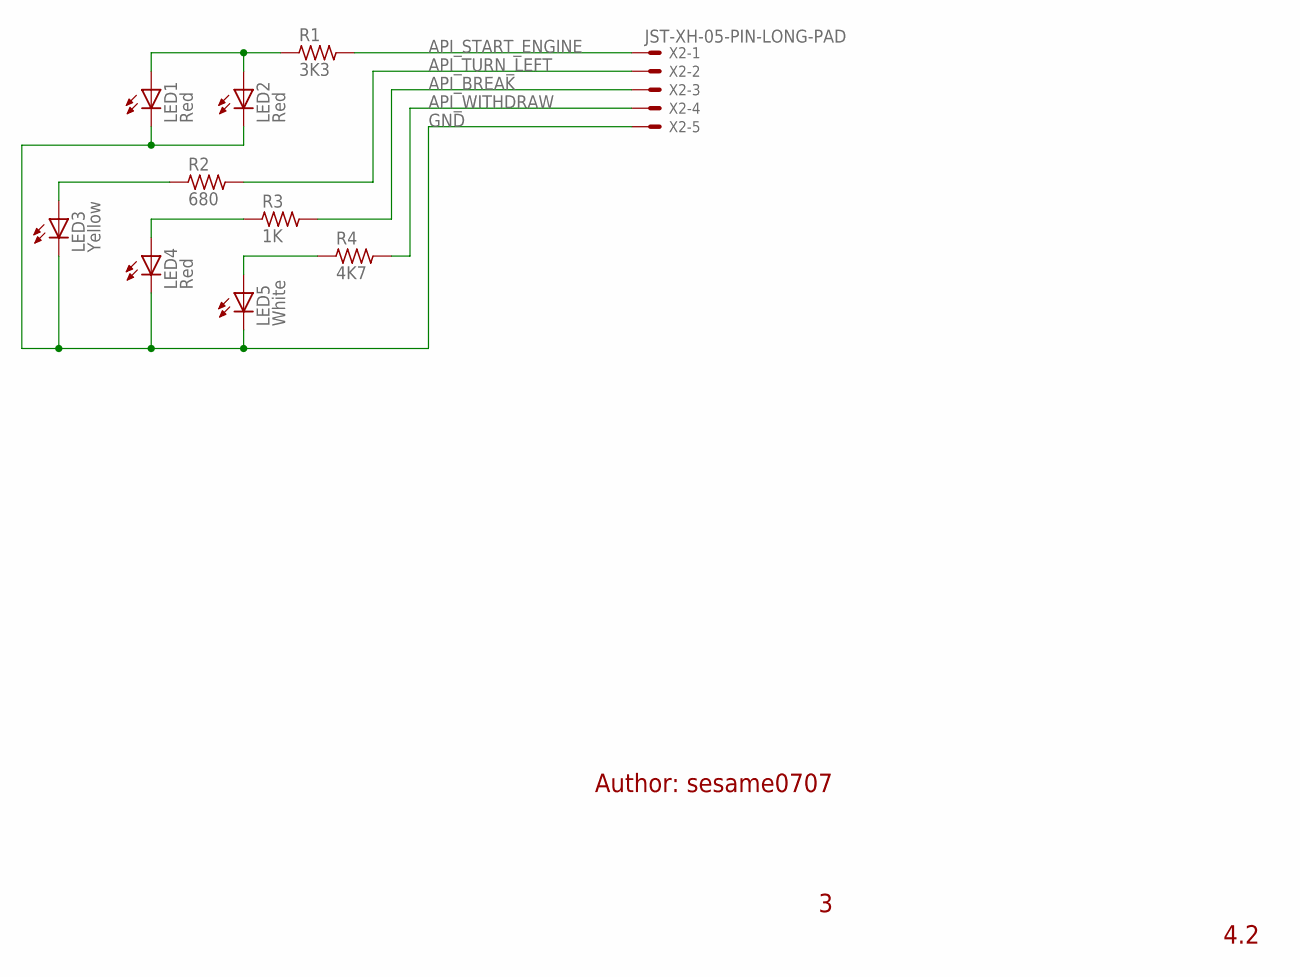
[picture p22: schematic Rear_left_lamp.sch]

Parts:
LED1, LED2, LED4: Red; LED5MM; VOLTAGE_EMPIRICAL 1.83 V; MANUFACTURER_PART_NUMBER LL-503VD2E-1B
LED3: Yellow; LED5MM; VOLTAGE_EMPIRICAL 1.88 V; MANUFACTURER_PART_NUMBER LL-503YD2E-1B
LED5: White; LED5MM; VOLTAGE_EMPIRICAL 2.58 V; MANUFACTURER_PART_NUMBER LL-504WC2V-W2-3PD
R1: 3K3; R1206; MANUFACTURER_PART_NUMBER 1206S4J0332T5E
R2: 680; R1206; MANUFACTURER_PART_NUMBER 1206S4J0681T5E
R3: 1K; R1206; MANUFACTURER_PART_NUMBER 1206S4J0102T5E
R4: 4K7; R1206; MANUFACTURER_PART_NUMBER 1206S4J0472T5E
X2: JST-XH-05-PIN-LONG-PAD; JST-XH-05-PACKAGE-LONG-PAD

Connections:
API_BREAK: R3.2, X2.3
API_START_ENGINE: LED1.A, LED2.A, R1.1
API_TURN_LEFT: R2.2, X2.2
API_WITHDRAW: R4.2, X2.4
GND: LED1.K (C), LED2.K (C), LED3.K (C), LED4.K (C), LED5.K (C), X2.5
unnamed: LED3.A, R2.1
unnamed: R1.2, X2.1
unnamed: LED4.A, R3.1
unnamed: LED5.A, R4.1

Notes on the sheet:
Author: sesame0707
4.2

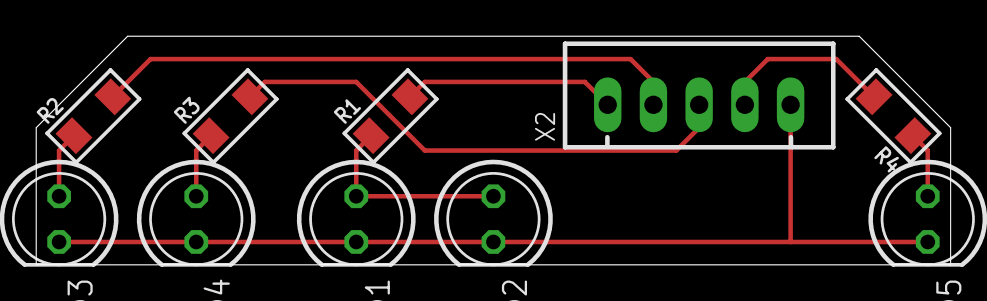
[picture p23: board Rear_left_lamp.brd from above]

Board: 2 copper layers, 50.8 x 12.7 mm, 10 parts (0 on the bottom side), 9 nets.

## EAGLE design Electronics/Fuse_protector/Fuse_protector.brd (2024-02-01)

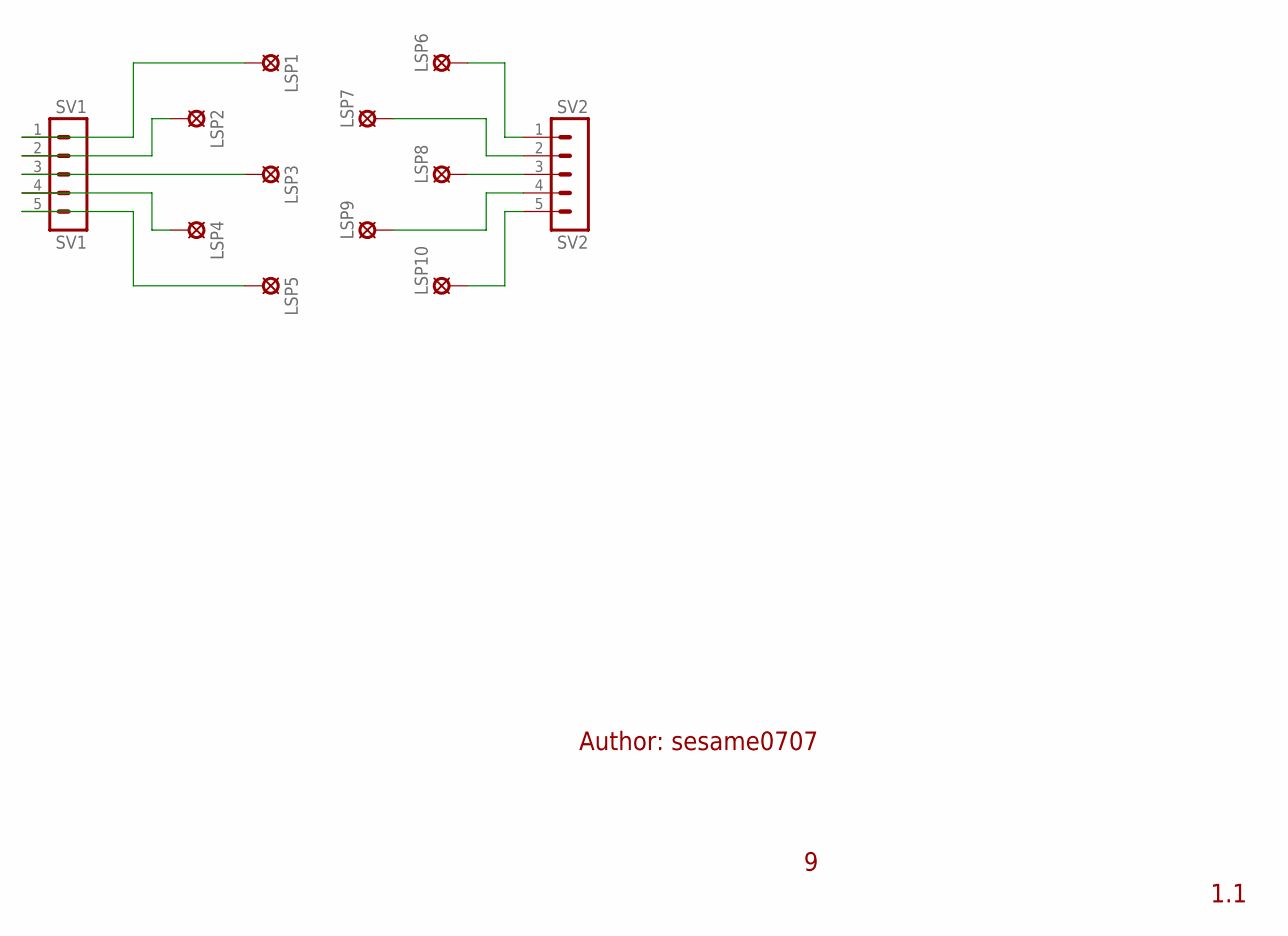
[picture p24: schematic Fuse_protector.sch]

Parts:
LSP1, LSP2, LSP3, LSP4, LSP5, LSP6, LSP7, LSP8, LSP9, LSP10: SE14
SV1: SV1; MA05-1
SV2: SV2; MA05-1

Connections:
unnamed: LSP1.MP, SV1.1
unnamed: LSP2.MP, SV1.2
unnamed: LSP3.MP, SV1.3
unnamed: LSP4.MP, SV1.4
unnamed: LSP5.MP, SV1.5
unnamed: LSP6.MP, SV2.1
unnamed: LSP7.MP, SV2.2
unnamed: LSP8.MP, SV2.3
unnamed: LSP9.MP, SV2.4
unnamed: LSP10.MP, SV2.5

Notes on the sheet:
Author: sesame0707
1.1

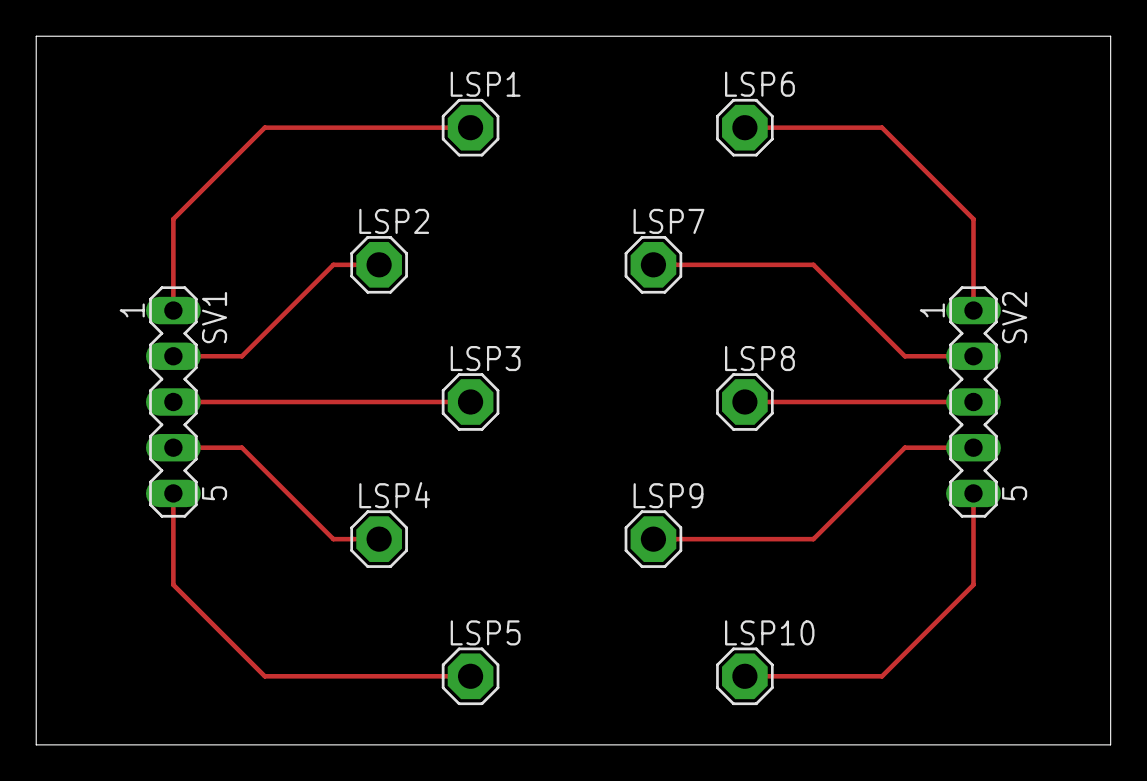
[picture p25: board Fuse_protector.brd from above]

Board: 2 copper layers, 59.7 x 39.4 mm, 12 parts (0 on the bottom side), 10 nets.

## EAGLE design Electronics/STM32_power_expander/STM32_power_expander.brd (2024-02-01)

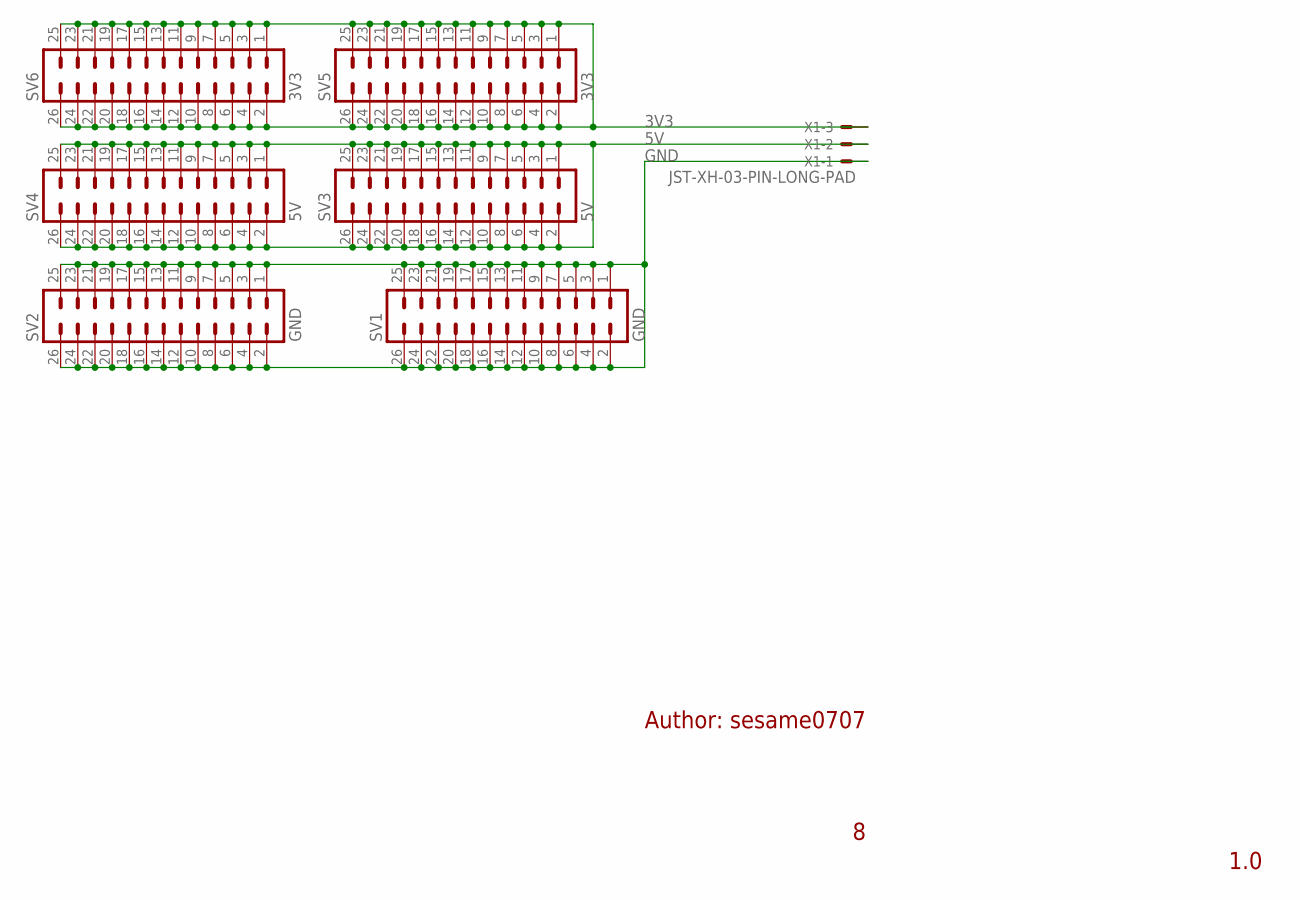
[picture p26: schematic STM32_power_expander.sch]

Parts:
SV1, SV2: GND; MA13-2
SV3, SV4: 5V; MA13-2
SV5, SV6: 3V3; MA13-2
X1: JST-XH-03-PIN-LONG-PAD; JST-XH-03-PACKAGE-LONG-PAD

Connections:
3V3: SV5.1, SV5.2, SV5.3, SV5.4, SV5.5, SV5.6, SV5.7, SV5.8, SV5.9, SV5.10, SV5.11, SV5.12, SV5.13, SV5.14, SV5.15, SV5.16, SV5.17, SV5.18, SV5.19, SV5.20, SV5.21, SV5.22, SV5.23, SV5.24, SV5.25, SV5.26, SV6.1, SV6.2, SV6.3, SV6.4, SV6.5, SV6.6, SV6.7, SV6.8, SV6.9, SV6.10, SV6.11, SV6.12, SV6.13, SV6.14, SV6.15, SV6.16, SV6.17, SV6.18, SV6.19, SV6.20, SV6.21, SV6.22, SV6.23, SV6.24, SV6.25, SV6.26, X1.3
5V: SV3.1, SV3.2, SV3.3, SV3.4, SV3.5, SV3.6, SV3.7, SV3.8, SV3.9, SV3.10, SV3.11, SV3.12, SV3.13, SV3.14, SV3.15, SV3.16, SV3.17, SV3.18, SV3.19, SV3.20, SV3.21, SV3.22, SV3.23, SV3.24, SV3.25, SV3.26, SV4.1, SV4.2, SV4.3, SV4.4, SV4.5, SV4.6, SV4.7, SV4.8, SV4.9, SV4.10, SV4.11, SV4.12, SV4.13, SV4.14, SV4.15, SV4.16, SV4.17, SV4.18, SV4.19, SV4.20, SV4.21, SV4.22, SV4.23, SV4.24, SV4.25, SV4.26, X1.2
GND: SV1.1, SV1.2, SV1.3, SV1.4, SV1.5, SV1.6, SV1.7, SV1.8, SV1.9, SV1.10, SV1.11, SV1.12, SV1.13, SV1.14, SV1.15, SV1.16, SV1.17, SV1.18, SV1.19, SV1.20, SV1.21, SV1.22, SV1.23, SV1.24, SV1.25, SV1.26, SV2.1, SV2.2, SV2.3, SV2.4, SV2.5, SV2.6, SV2.7, SV2.8, SV2.9, SV2.10, SV2.11, SV2.12, SV2.13, SV2.14, SV2.15, SV2.16, SV2.17, SV2.18, SV2.19, SV2.20, SV2.21, SV2.22, SV2.23, SV2.24, SV2.25, SV2.26, X1.1

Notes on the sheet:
Author: sesame0707
1.0

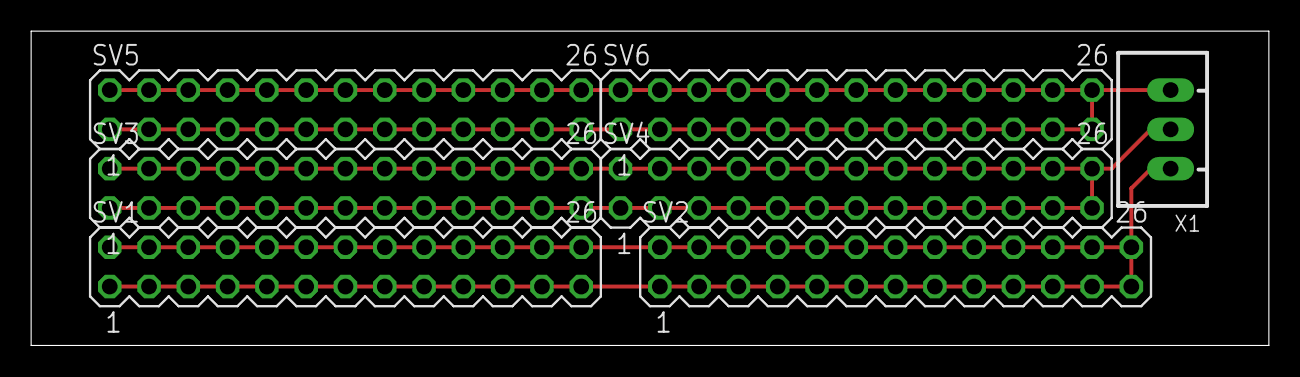
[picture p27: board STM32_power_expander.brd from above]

Board: 2 copper layers, 80.0 x 20.3 mm, 7 parts (0 on the bottom side), 3 nets.

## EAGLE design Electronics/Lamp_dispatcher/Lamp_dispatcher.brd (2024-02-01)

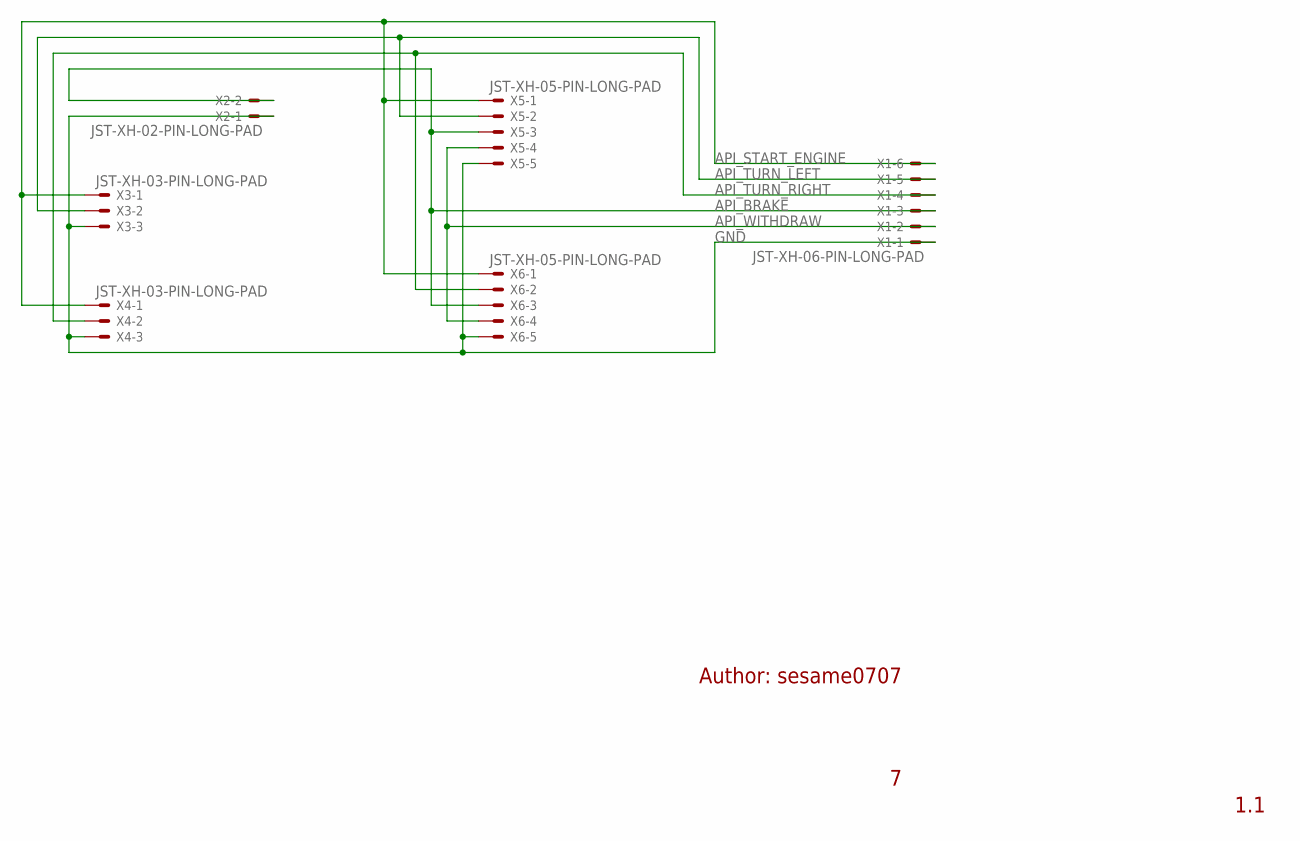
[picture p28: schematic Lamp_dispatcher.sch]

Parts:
X1: JST-XH-06-PIN-LONG-PAD; JST-XH-06-PACKAGE-LONG-PAD
X2: JST-XH-02-PIN-LONG-PAD; JST-XH-02-PACKAGE-LONG-PAD
X3, X4: JST-XH-03-PIN-LONG-PAD; JST-XH-03-PACKAGE-LONG-PAD
X5, X6: JST-XH-05-PIN-LONG-PAD; JST-XH-05-PACKAGE-LONG-PAD

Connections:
API_BRAKE: X1.3, X2.2, X5.3, X6.3
API_START_ENGINE: X1.6, X3.1, X4.1, X5.1, X6.1
API_TURN_LEFT: X1.5, X3.2, X5.2
API_TURN_RIGHT: X1.4, X4.2, X6.2
API_WITHDRAW: X1.2, X5.4, X6.4
GND: X1.1, X2.1, X3.3, X4.3, X5.5, X6.5

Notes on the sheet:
Author: sesame0707
1.1

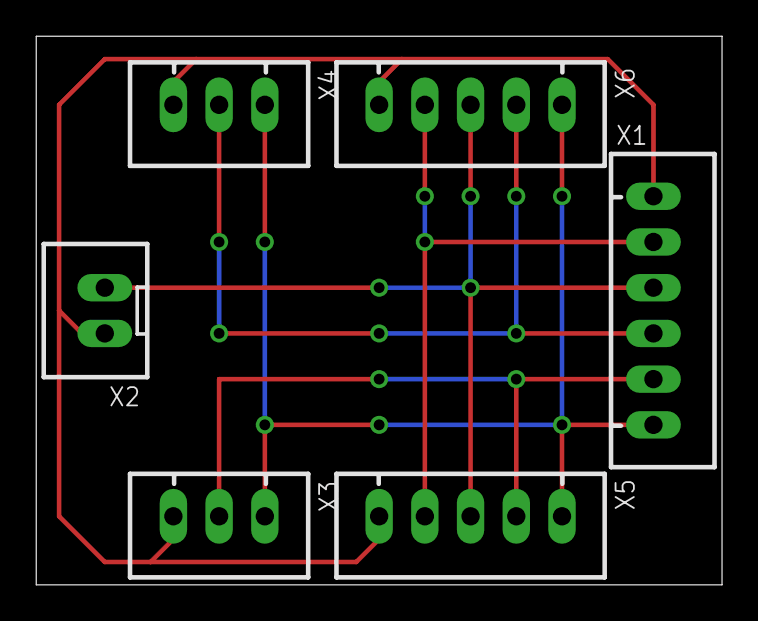
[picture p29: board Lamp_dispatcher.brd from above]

Board: 2 copper layers, 38.1 x 30.5 mm, 6 parts (0 on the bottom side), 6 nets.

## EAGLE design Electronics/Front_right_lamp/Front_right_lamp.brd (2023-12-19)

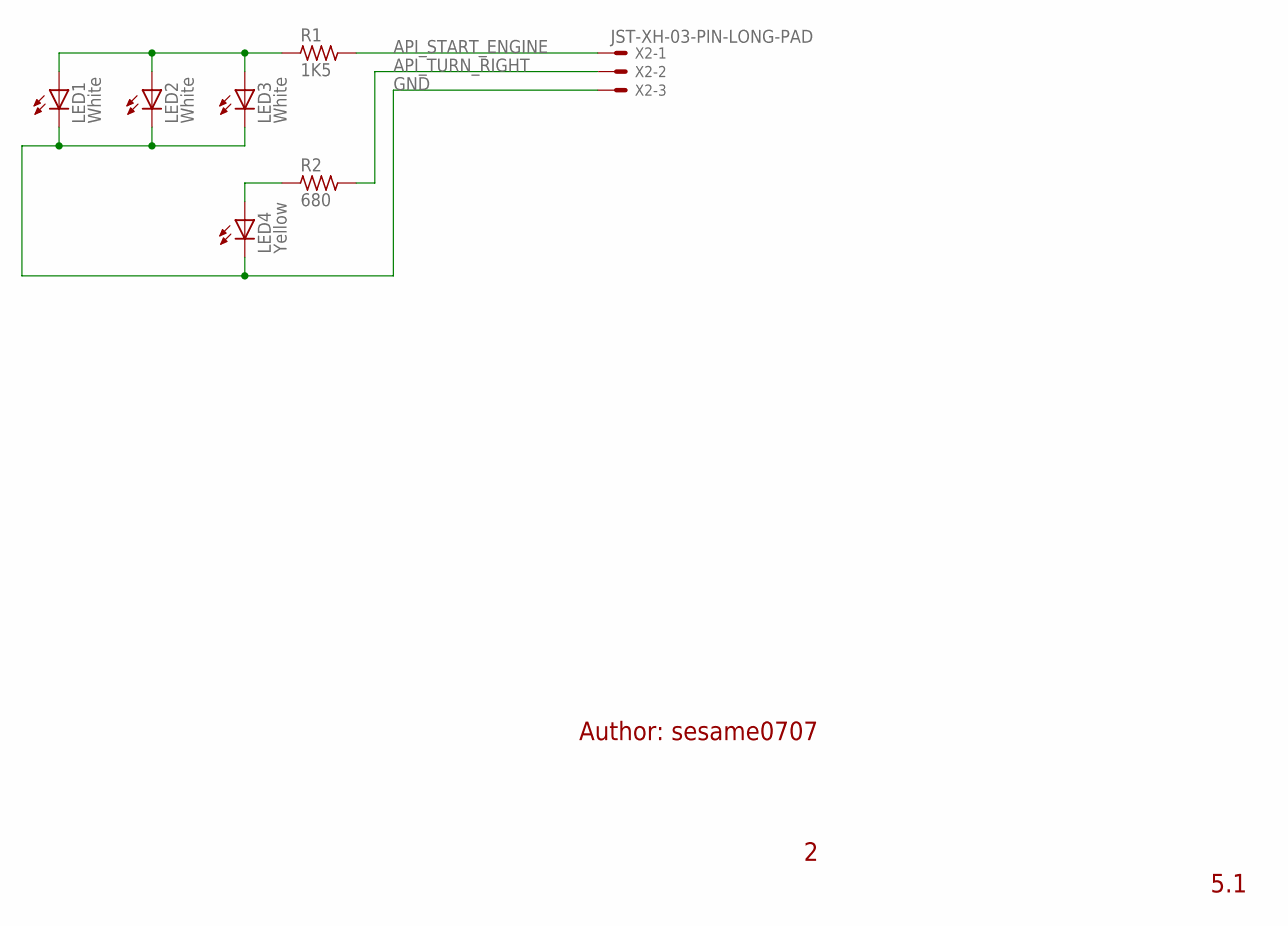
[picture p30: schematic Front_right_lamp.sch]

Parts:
LED1, LED2, LED3: White; LED5MM; VOLTAGE_EMPIRICAL 2.58 V; MANUFACTURER_PART_NUMBER LL-504WC2V-W2-3PD
LED4: Yellow; LED5MM; VOLTAGE_EMPIRICAL 1.88 V; MANUFACTURER_PART_NUMBER LL-503YD2E-1B
R1: 1K5; R1206; MANUFACTURER_PART_NUMBER 1206S4J0152T5E
R2: 680; R1206; MANUFACTURER_PART_NUMBER 1206S4J0681T5E
X2: JST-XH-03-PIN-LONG-PAD; JST-XH-03-PACKAGE-LONG-PAD

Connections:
API_START_ENGINE: LED1.A, LED2.A, LED3.A, R1.1
API_TURN_RIGHT: R2.2, X2.2
GND: LED1.K (C), LED2.K (C), LED3.K (C), LED4.K (C), X2.3
unnamed: LED4.A, R2.1
unnamed: R1.2, X2.1

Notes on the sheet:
Author: sesame0707
5.1

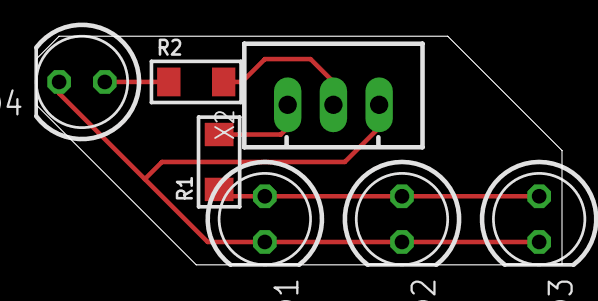
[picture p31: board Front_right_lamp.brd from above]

Board: 2 copper layers, 29.2 x 12.7 mm, 7 parts (0 on the bottom side), 5 nets.

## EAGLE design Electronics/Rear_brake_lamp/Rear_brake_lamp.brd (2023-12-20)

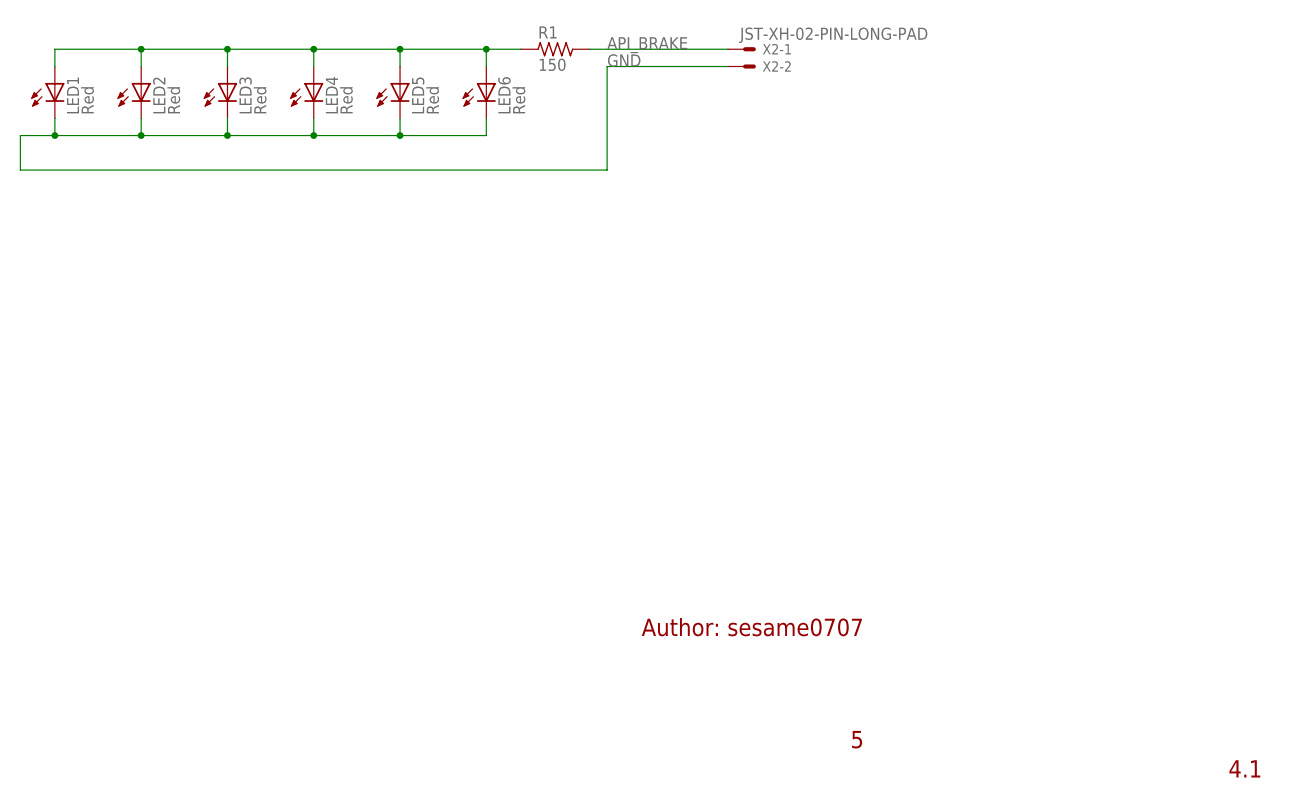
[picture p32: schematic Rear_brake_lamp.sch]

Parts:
LED1, LED2, LED3, LED4, LED5, LED6: Red; LED5MM; VOLTAGE_EMPIRICAL 1.83 V; MANUFACTURER_PART_NUMBER LL-503VD2E-1B
R1: 150; R1206; MANUFACTURER_PART_NUMBER 1206S4J0151T5E
X2: JST-XH-02-PIN-LONG-PAD; JST-XH-02-PACKAGE-LONG-PAD

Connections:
API_BRAKE: LED1.A, LED2.A, LED3.A, LED4.A, LED5.A, LED6.A, R1.1
GND: LED1.K (C), LED2.K (C), LED3.K (C), LED4.K (C), LED5.K (C), LED6.K (C), X2.2
unnamed: R1.2, X2.1

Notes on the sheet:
Author: sesame0707
4.1

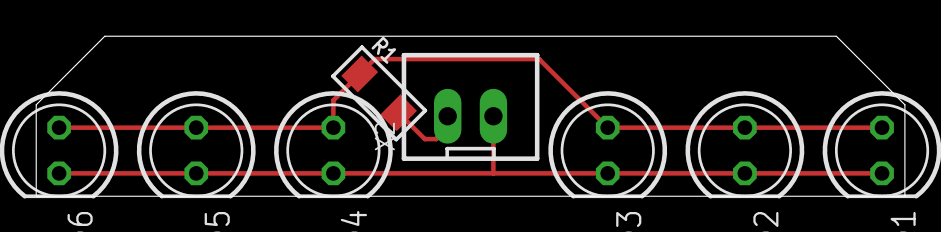
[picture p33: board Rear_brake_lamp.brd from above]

Board: 2 copper layers, 48.3 x 8.9 mm, 8 parts (0 on the bottom side), 3 nets.

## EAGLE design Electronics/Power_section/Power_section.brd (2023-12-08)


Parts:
BATTERY_+, BATTERY_+1: WIREPADSMD2,54-5,08; SMD2,54-5,08
BATTERY_-, BATTERY_-1: WIREPADSMD2,54-5,08; SMD2,54-5,08
BLDC_MOTOR_IN: AK500/2
BLDC_MOTOR_OUT: AK500/2
FUSE_IN: SE14
FUSE_OUT: SE14
LED_STRIPE_POWER: AK500/2
RPI_PICO_W_POWER: AK500/2
SAFETY_SWITCH_IN: AK500/2
SAFETY_SWITCH_OUT: AK500/2
STEPPER_MOTOR_IN: AK500/2
STM32_NUCLEO_POWER: AK500/2

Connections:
5V: BLDC_MOTOR_OUT.2, LED_STRIPE_POWER.2, RPI_PICO_W_POWER.2, STM32_NUCLEO_POWER.2
12V: FUSE_OUT.MP, SAFETY_SWITCH_IN.1, SAFETY_SWITCH_IN.2
BLDC_MOTOR: BLDC_MOTOR_IN.1, SAFETY_SWITCH_OUT.1
GND: BATTERY_-.1, BATTERY_-1.1, BLDC_MOTOR_IN.2, BLDC_MOTOR_OUT.1, LED_STRIPE_POWER.1, RPI_PICO_W_POWER.1, STEPPER_MOTOR_IN.2, STM32_NUCLEO_POWER.1
unnamed: BATTERY_+.1, BATTERY_+1.1, FUSE_IN.MP
STEPPER_MOTOR: SAFETY_SWITCH_OUT.2, STEPPER_MOTOR_IN.1

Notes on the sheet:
Author: sesame0707
1.2


Board: 2 copper layers, 33.0 x 47.0 mm, 14 parts (0 on the bottom side), 6 nets.

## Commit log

2023-08-17 Added list of parts and official LEGO manuals
    [List of parts.xlsx]
2023-08-23 List of parts updated
    [List of parts.xlsx]
2023-08-29 LED stripe tested
    [List of parts.xlsx]
2023-10-11 LEDs test project done
    [LEDs_1.sch]
2023-10-13 Front_left_lamp done
    [Front_left_lamp_v1.brd, Front_left_lamp_v1.sch]
2023-10-23 Front lamps done
    [Front_left_lamp_v1.brd, Front_left_lamp_v1.sch, Front_left_lamp_v2.brd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]
2023-10-23 Front and rear lamps done
    [Front_left_lamp_v2.brd, Front_left_lamp_v2.sch, Front_right_lamp_v2.brd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]
2023-10-27 Rear brake lamp started
    [LEDs_v1.brd, LEDs_v1.sch, Rear_brake_lamp_v1.brd]
2023-10-29 Rear brake lamp done
    [Rear_brake_lamp_v1.brd]
2023-10-31 Rear lamps improved
    Greater resistors' value for API_START_ENGINE
    [Rear_left_lamp_v1.brd, Rear_left_lamp_v1.sch, Rear_right_lamp_v1.brd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]
2023-11-12 All lamps improved
    Refactoring into only "top" layer done
    [Front_left_lamp_v3.brd, Front_left_lamp_v3.sch, Front_right_lamp_v3.brd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]
2023-11-18 All lamps improved
    Refactoring into less, but more powerful resistors done
    [Front_left_lamp_v4.brd, Front_left_lamp_v4.sch, Front_right_lamp_v4.brd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]
2023-11-18 Tests folder removed
    [Irregular_board_v1.brd, Irregular_board_v1.sch, LEDs_v1.brd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]
2023-11-23 Split into "Regular" and "For LPKF milling machine" branches done
    [Front_left_lamp_v1.brd, Front_left_lamp_v1.sch, Front_left_lamp_v2.brd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]
2023-12-07 Power section done
    [Power_section_v1.brd, Power_section_v1.sch]
2023-12-07 All lamps improved
    Refactoring includes:
    - dimension minimalization,
    - removal of the common ground plane,
    - anti-short circuit placement of components,
    - replacement of round pads with the long ones
    [Front_left_lamp_v5.brd, Front_left_lamp_v5.sch, Front_right_lamp_v5.brd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]
2023-12-08 Power section improved
    What has been improved:
    - changed fuse holder slot for the smaller model,
    - made wires wider
    [Power_section_v1.brd, Power_section_v1.sch]
2023-12-08 Power section improved
    - moved BAT+ and BAT- pads to the very left,
    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
    [Power_section_v1.brd, Power_section_v1.sch]
2023-12-11 Export for milling done
    [Front_left_lamp_v5.drl, Front_right_lamp_v5.drl, Power_section_v1.drl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]
2023-12-19 BOM on front lamps added
    [Front_left_lamp_v5.brd, Front_left_lamp_v5.sch, Front_right_lamp_v5.brd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]
2023-12-20 BOM on all the lamps added
    Note: Version of lamps' projects has increased from x.0 to x.1.
    What also has been done:
    - some visual refactoring on schematics
    [Front_right_lamp_v5.sch, Rear_brake_lamp_v4.brd, Rear_brake_lamp_v4.sch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]
2023-12-20 Transition to revision-only versioning system done
    [Front_left_lamp.brd, Front_left_lamp.sch, Front_left_lamp_v1.brd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]
2024-01-25 Lamp dispatcher done
    [Lamp_dispatcher.brd, Lamp_dispatcher.sch]
2024-02-01 Lamp dispatcher improved
    - rotated 2- and 6-pin JST connectors,
    - corrected PCB dimensions,
    - curved GND wire
    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
    [Lamp_dispatcher.brd, Lamp_dispatcher.sch]
2024-02-01 Fuse protector done
    [Fuse_protector.brd, Fuse_protector.sch]
2024-02-01 STM32 power expander done
    [STM32_power_expander.brd, STM32_power_expander.sch]
2024-02-01 Components' power draw updated
2024-02-01 Fuse protector improved
    - corrected size of space for fuses
    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
    [Fuse_protector.brd, Fuse_protector.sch]
2024-02-03 Rear lamps improved
    - changed API_START_ENGINE red LEDs' CURRENT_EMPIRICAL value one decimal point smaller
    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
    [Rear_left_lamp.brd, Rear_left_lamp.sch, Rear_right_lamp.brd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]
2024-02-15 Battery information file added
    [Battery information.xlsx]
2024-02-16 Battery percentage order reversed
    [Battery information.xlsx]
2024-02-19 Files' rearrangement done
    [Battery information.xlsx, List of parts.xlsx]
2024-02-19 Li-Po battery voltage characteristics added
2024-02-20 .gitignore file implemented
    [Front_left_lamp_v5.drl, Front_right_lamp_v5.drl, Power_section_v1.drl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]
2024-02-22 List of parts updated
    Refactoring also has been done
    [List of parts.xlsx]
2024-02-23 Components' power draw updated
    Measured RPi's power draw under load
2024-03-06 Components' power draw updated
    Measured battery charge level indicators' power draw and updated total power draw
2024-03-06 Battery charged
    [Battery information.xlsx]
2024-04-08 Part "1. Stepper motor holder (L)" done
    [1. Stepper motor holder (L) [V1].f3d, 1. Stepper motor holder (L) [V1].stl, 1. Stepper motor holder (L) [V2].f3d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]
2024-04-10 Part "2. Stepper motor holder (R)" done
    [2. Stepper motor holder (R) [V4].f3d, 2. Stepper motor holder (R) [V4].stl]
2024-04-11 Part "3. BLDC motor holder" done
    [3. BLDC motor holder [V1].f3d, 3. BLDC motor holder [V1].stl]
2024-04-11 Part "4. BLDC motor transmission 7x bar" done
    [4. BLDC motor transmission 7x bar [V1].f3d, 4. BLDC motor transmission 7x bar [V1].stl]
2024-04-12 Part "3. BLDC motor holder" improved
    [3. BLDC motor holder [V2].f3d, 3. BLDC motor holder [V2].stl, 3. BLDC motor holder [V3].f3d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]
2024-04-19 File arrangement done
    [List of parts.xlsx]

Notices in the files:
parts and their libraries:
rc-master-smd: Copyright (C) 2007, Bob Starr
